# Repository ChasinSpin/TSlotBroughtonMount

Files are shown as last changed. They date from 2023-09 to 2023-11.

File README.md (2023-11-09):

# T-Slot Broughton Mount

#### Author: ChasinSpin

The T-Slot Broughton Mount is a fixed-position AltAz telescope mount designed primarily for pre-point asteroid occultations with smaller telescopes. It is similar to a tripod, but easier and more precise when adjusting. Better than 1-arcmin precision is easily achievable in practice.

This mount is inspired by the original Paver Mount design of John Broughton and has similar dimensions.

The design uses 2020 Aluminum T-Slot, 3D-Printed parts, and is easy to build.

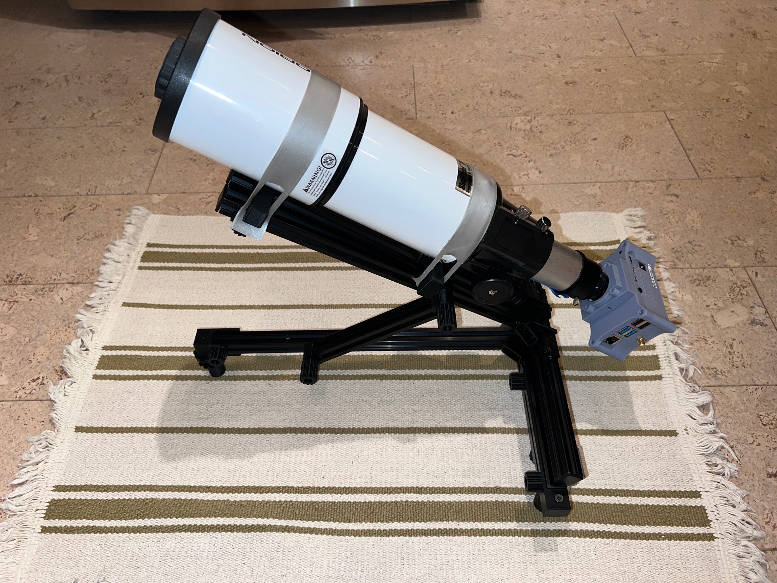
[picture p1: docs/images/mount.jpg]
T-Slot Broughton Mount


##### Overview:

* [Features](#features)
* [Supported Telescopes](#supported-telescopes)
* [Printing 3D Parts](#printing-3d-parts)
* [Azimuth Adjustment](#azimuth-adjustment)
* [Altitude Adjustment](#altitude-adjustment)
* [Collapsing For Transport](#collapsing-for-transport)
* [Marking Settings For Later Deployment](#marking-settings-forlater-deployment)
* [Attaching Telescopes](#attaching-telescopes)
* [High Altitudes near Zenith](#high-altitudes-near-zenith)
* [Use With 12inch Pavers](#use-with-12inch-pavers)
* [Extending For Larger Scopes](#extending-for-larger-scopes)
* [Paver Registration](#paver-registration)
* [Repeatability](repeatability)
* [Anti-Tip-Over Bar](anti-tip-over-bar)
* [Parts List](#parts-list)
* [Add-Ons](#add-ons)

##### Guides:

* [Assembly Guide](docs/assemblyguide.md)
* [Usage Guide](#usage-guide)

## Features

* Low profile
* Parametric design in [OpenSCAD](https://openscad.org). Can easily be adapted. 
* Full range (0-90 degrees in altitude - zenith works)
* Small and lightweight (3lb/1.375kg), ideal for air travel (can also be disassembled)
* Supports "pre-point later". (Set up, remove, and place back in position days later)
* Collapsable for transport (and can be put back to the previous AltAz position)
* Both coarse and fine adjustments for altitude and azimuth
* Rigid design
* Silver or black (black for stealth deployments)
* 2020 Aluminum T-Slot, using standard parts
* Easy to build (hacksaw, file, drill, 3D printed parts)
* Can be used with a 12" or 16" paver, staked piece of plywood for pre-positioning days prior
* Anti Tip-Over Bar
* Cost-effective
* Can be adjusted to better than 1-arcmin precision

## Supported Telescopes

Many small telescopes are supported, for example:

* Mighty Mini (IOTA) - (1/4-20 UNC standard tripod thread)
* Orion ST (Short Tube) 80mm
* If the scope is larger, the design can be expanded, see [Extending For Larger Scopes](extending-for-larger-scopes)

The [Astrid](https://github.com/ChasinSpin/astrid) astro imaging device is also supported.

## Printing 3D Parts

If you have a 3D filament printer, then you're good to go. It's also possible to order the parts printed for you via a 3D printing service. The parts are designed to be printed in PLA, but other materials can be used.

[STL Files](stl)

## Azimuth Adjustment

Coarse azimuth adjustments can be made by rotating the mount on the surface it's standing on.  Fine adjustments can be made with 2 fingers pushing against the 2 pieces of 2020 to displace the position and the thumbwheel can be used to tighten.

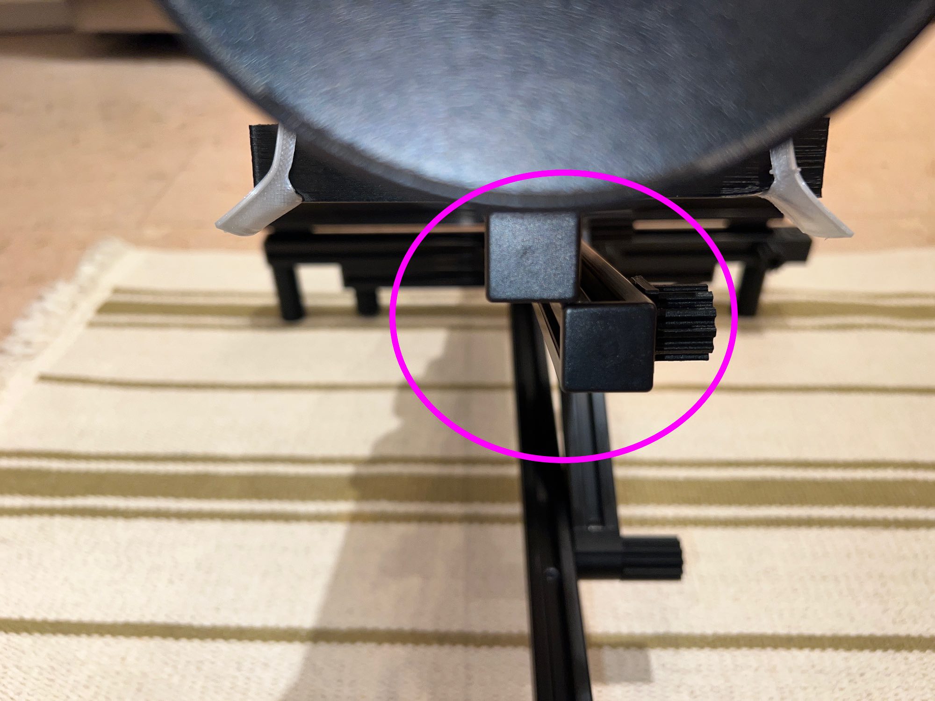
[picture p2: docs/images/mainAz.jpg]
Azimuth Adjustment


## Altitude Adjustment

Coarse altitude adjustments can be made by raising/lowering the altitude bar and tightening the knobs.  Fine adjustments can be made by using the screw in the foot at the front of the mount.

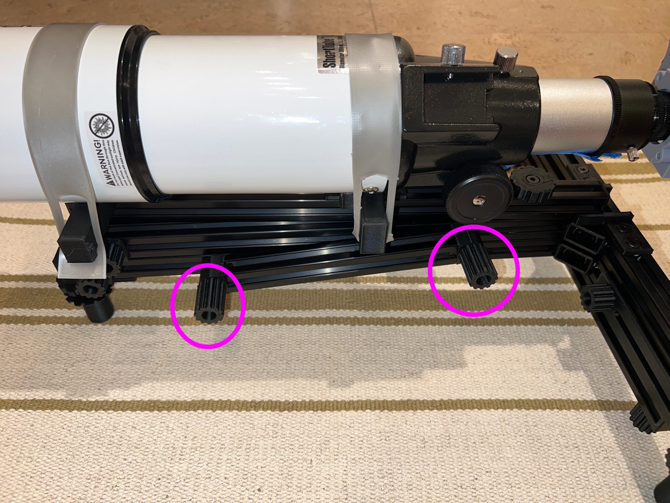
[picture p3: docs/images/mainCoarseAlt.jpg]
Coarse Altitude Adjustment

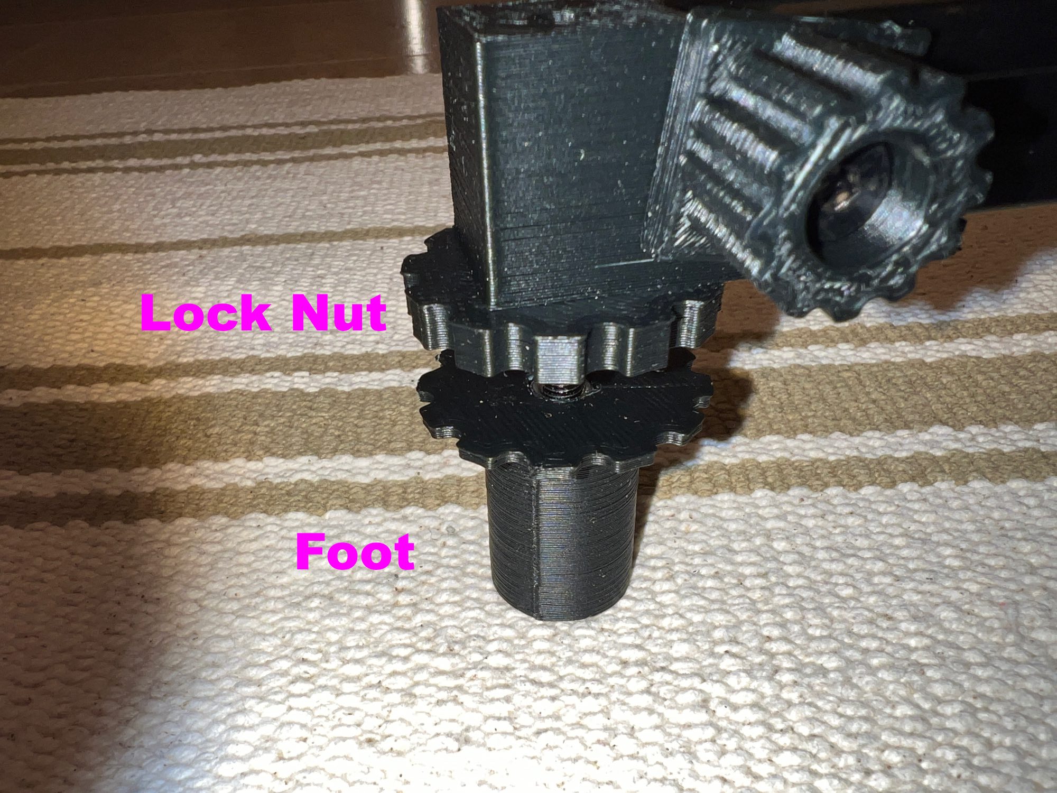
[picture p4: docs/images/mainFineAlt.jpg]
Fine Altitude Adjustment


## Collapsing For Transport

The mount can be completely collapsed for transport.  Additionally, if air traveling and an extremely minimal footprint is required, an Allen key can be used to detach the cross bars for transport.

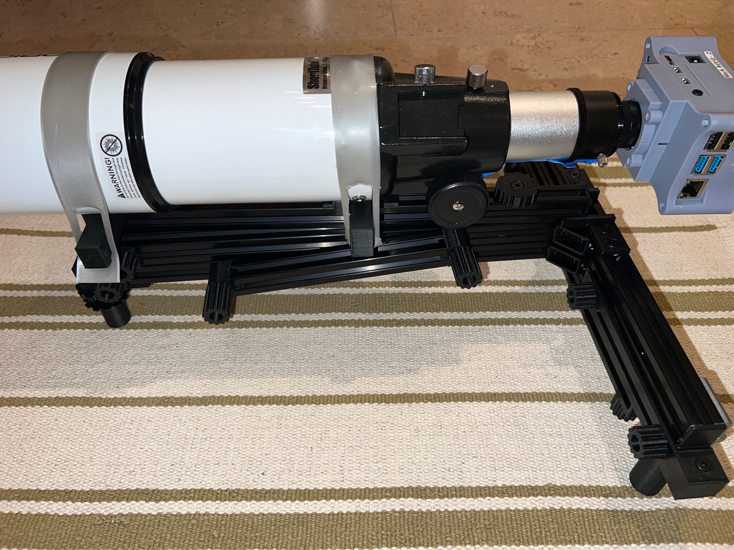
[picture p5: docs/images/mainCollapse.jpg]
Collapsed


## Marking Settings For Later Deployment

Move the altitude position markers up against the altitude bar to save the position, and tighten and disconnect the altitude bar.

An alternative is to use a 0.4mm Sharpie felt pen to mark the position of both ends of the altitude bar on the aluminum.  To remove the marking later, any type of alcohol can be used to remove.

The altitude fine adjustment foot can be locked in place using the lock wheel provided.

For azimuth, use the graduated scale near the front of the mount, and note the position (or take a photo).  Alternatively, calipers can be used to note the measurement for later.

## Attaching Telescopes

Telescopes can be attached via a stretchable band 3d printed from NinjaFlex or TPU.  Also, just a length of TPU/NinjaFlex filament, thick rubber band or strong elastic can be used.

## High Altitudes near Zenith

Due to the weight of the scope and the possibility of tip-over, for higher altitudes nearer to the zenith, the anti-tip-over bar should be swung out to prevent tip-over.  See [Anti-Tip-Over Bar](#anti-tip-over-bar)

## Use With 12inch Pavers

The original paver mount has its feet removed for placement on a 12-inch paver as the mount is larger than the paver.  The T-Slot Broughton Mount can be used the same way by removing the rear feet. Next, remove the front foot, and insert backward through the hole and T-Nut further back along the T-Slot to retain the fine altitude adjustment.

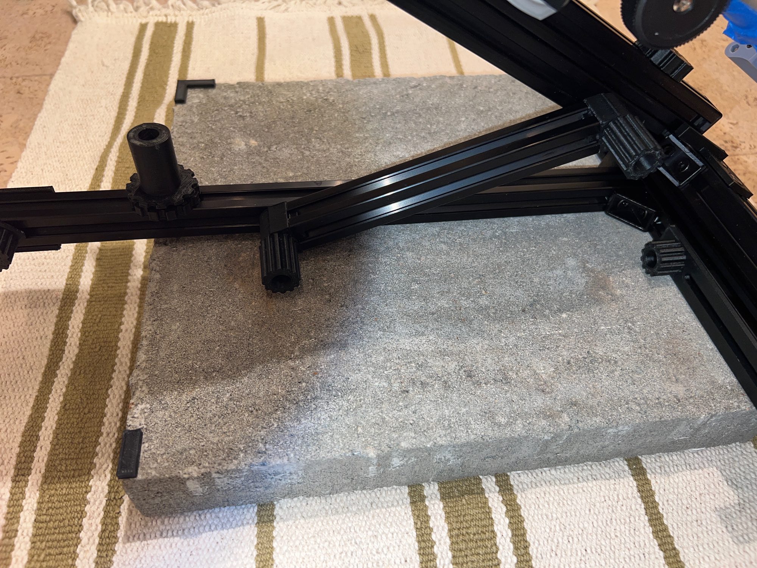
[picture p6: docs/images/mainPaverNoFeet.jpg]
Paver Without Feet


Another (better) option is to slide the rear feet so they are just under 12 inches apart.  Remove the Front Foot Lock from the Front Foot and insert the Front Foot into the hole and T-Nut further back from the front foot's regular location.  Now use the Front Foot Lock on top of the 2020 to lock down/remove play in the Front Foot.

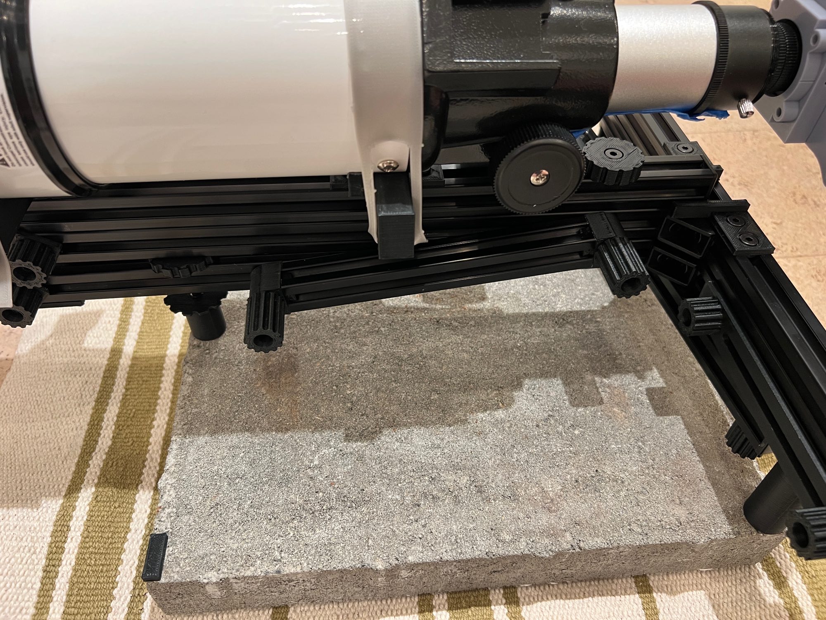
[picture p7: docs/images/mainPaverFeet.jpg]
Paver With Feet


To prevent tip over at high elevations with 12-inch paver, it's recommended to use the [Battery Platform](addons/BatteryPlatform/README.md).

## Extending For Larger Scopes

The design is extendable within sensible limits for larger telescopes, by increasing the length of the 2020 extrusion for parts ABC.

Extending

## Paver Registration

Repeatable registration of the mount feet with the paver can be accomplished by epoxying or super-gluing the paver makers at the edges of the paver.  Place the right-angled marker against the left corner and the straight marker against the same edge such that the left rear foot of the mount fits in the right-angled marker, and the right rear foot of the mount rests against the straight marker.

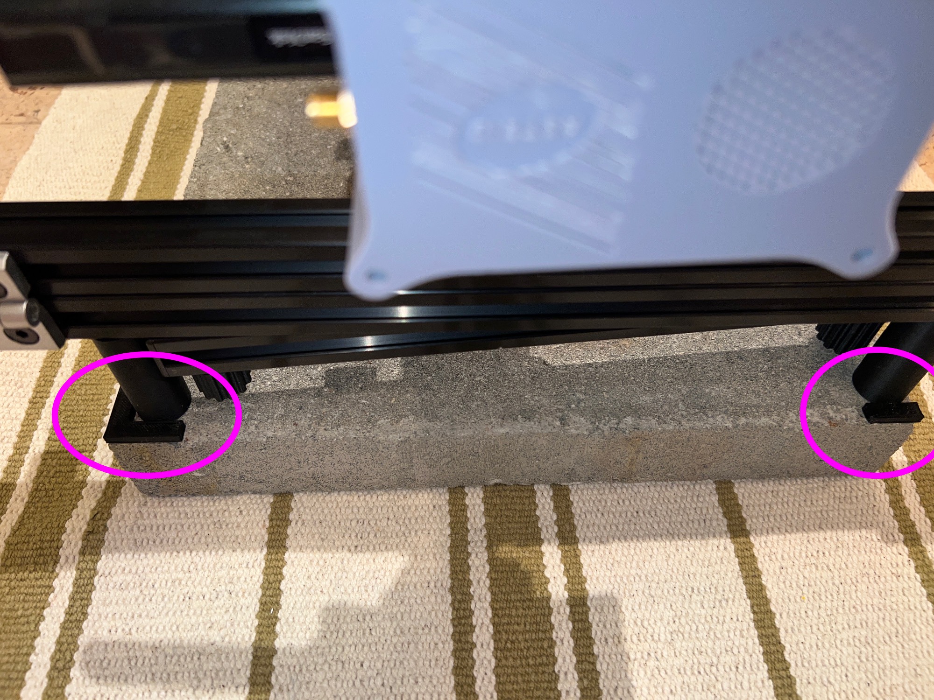
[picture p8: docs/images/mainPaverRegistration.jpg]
Paver Registration


## Repeatability

The following testing is with an Orion ST 80mm and IOTA Focal Reducer 0.5X with focal length 185mm and 1.543x1.154deg FOV.

**Initial** refers to the error after adjusting the mount to the pre-point location.  **Reposition** are subsequent measurements after repositioning the mount.

**Error Az/Alt** are in arc minutes and are the difference between where the telescope is pointing and the pre-point location of the target at that time.  **Error FOV** is the same error represented as a percentage of the Field of View, where the height of the field of view is 100%.

### Testing repeatability in pre-pointing with Astrid

After initial pre-point alignment and lockdown of the mount, the scope was picked up with the mount and placed back on the paver, to simulate a pre-point where the setup is removed and replaced days later.

| Step | Error Az (arcmin) | Error Alt (arcmin) | Error FOV |
| ---- | --- | --- | --- |
| Initial | -0.582 | -0.995 | 1.4% |
| Reposition | -3.690 | +0.638 | 5.3% |
| Reposition | -1.971 | +1.373 | 2.8% |
| Reposition | -1.710 | +1.539 | 2.5% |
| Reposition | +0.489 | +2.634 | 3.8% |
| Reposition | -6.155 | +2.172 | 8.9% |
| Reposition | -5.880 | +2.691 | 8.5% |
| Reposition | +3.263 | +3.217 | 4.7% |

### Testing repeatability for "pre-point later" with Astrid after mount collapse and telescope removal for transport

After initial pre-point alignment, the telescope was removed from the mount,
and the mount collapsed for transport.  The altitude bar position was maintained via the altitude bar markers, and the azimuth scale was noted.  The setup was then reassembled and aligned with the paver.

| Step | Error Az (arcmin) | Error Alt (arcmin) | Error FOV |
| ---- | --- | --- | --- |
| Initial | | | |
| TESTING PENDING

## Anti-Tip-Over Bar

The design has an anti-tip-over bar that can be swung out to the rear of the scope to prevent tip-over of the scope at high elevations.  The anti-tip-over bar does not fit the 12-inch paver due to the paver's small size, for this scenario please use the [Battery Platform](addons/BatteryPlatform/README.md) instead.

The Anti-Tip-Over Bar is optional and can be omitted for many occultations.

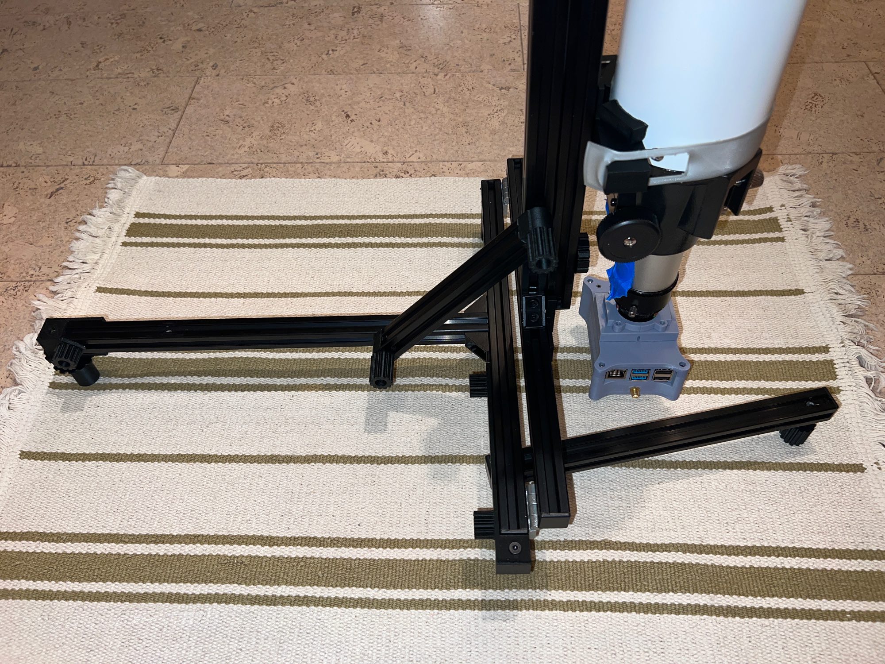
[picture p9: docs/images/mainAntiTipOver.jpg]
Anti-Tip-Over Bar


## Parts list

| Qty | Part | Description |
| --- | ---- | --- |
| 5 | 2020 x 360mm | [2020 EU STandard T-Slot](https://spool3d.ca/2020-aluminum-extrusion/) - 360mm Length (Silver or Black) |
| 1 | 2020 x 270mm | [2020 EU STandard T-Slot](https://spool3d.ca/2020-aluminum-extrusion/) - 270mm Length (Silver or Black) |
| 1 | 2020 x 160mm | [2020 EU STandard T-Slot](https://spool3d.ca/2020-aluminum-extrusion/) - 160mm Length (Silver or Black) |
| | | Note above T-Slot can be purchased as a 1 x 1.5m and 1 x 1m and cut to size or 3 x 1m | 
| 4 | 2020 Corner Bracket | [2020 Aluminum Corner Bracket Small](https://spool3d.ca/2020-aluminum-corner-bracket-small/) (Silver of Black) |
| 2 | 2020 Hinge | [2020 Aluminum Hinge](https://spool3d.ca/2020-aluminum-hinge/) (Silver or Black) |
| 28 | M5 x 8mm | [M5 Low Profile Bolt](https://spool3d.ca/m5-low-profile-screws/) - 8mm Length - Dimensions: (head diameter = 8.8mm, head thickness = 1.7mm) |
| 2 | M5 x 15mm | [M5 Low Profile Bolt](https://spool3d.ca/m5-low-profile-screws/) - 15mm Length - Dimensions: (head diameter = 8.8mm, head thickness = 1.7mm) |
| 4 | M5 x 35mm | [M5 Low Profile Bolt](https://spool3d.ca/m5-low-profile-screws/) - 35mm Length - Dimensions: (head diameter = 8.8mm, head thickness = 1.7mm) |
| 1 | M5 x 45mm | [M5 Low Profile Bolt](https://spool3d.ca/m5-low-profile-screws/) - 45mm Length - Dimensions: (head diameter = 8.8mm, head thickness = 1.7mm) |
| 1 | M5 x 50mm | [M5 Low Profile Bolt](https://spool3d.ca/m5-low-profile-screws/) - 50mm Length - Dimensions: (head diameter = 8.8mm, head thickness = 1.7mm) |
| 36 | M5 T-Nut | [M5 Sliding T-Nut](https://spool3d.ca/m5-sliding-t-nut/). Note, these are not twist in or "hammer head" T-Nuts, i.e. these are regular T-Nuts that won't fall out of the T-Slot.
| 10 | M5 Nut | M5 Nut - Dimensions: (diameter =  9mm point to point, thickness = 3.9mm) |
| 10 | End Cap | [Aluminum Extrusion Plastic Cap](https://spool3d.ca/aluminum-extrusion-plastic-cap/) |
| 1 | 3D Plate1 | Plate 1 3D-Printed Parts PLA |
| 1 | 3D Plate2 | Plate 2 3D-Printed Parts PLA |
| 1 | 3D Mount | 3D-Printed Mount PLA, e.g. Mount Orion ST 80mm or 1/4" Mount |
| 1 | 3D Bands | Bands 3D-Printed TPU/NinjaFlex to hold Orion ST 80mm telescope or strong rubber bands |
| 1 | 1/4-20 UNC Bolt | 1/4-20 UNC Bolt (regular tripod bolt) for 1/4 inch tripod mount if used) |
| 1 | Double Sided Tape | Permanent double-sided (e.g. Scotch Extreme Mounting Tape or Hot Glue) to attach telescope slide stops to telescope (Orion ST 80mm) |

**Note: All bolts are measured from the tip to the start of the head flange and do not include the thickness of the head.**

## Add-Ons

T-Slot is highly configurable.  If you design some fittings to work with this mount for telescopes, accessories, or anything else... please use [OpenSCAD](https://openscad.org) to design so that it is parametric and upload it to GitHub with a picture and README.md as a pull request, so others can benefit.  All submissions are assumed to be open source and under the MIT license.

[List of Add-Ons](/addons/README.md)

## Guides

* [Assembly Guide](docs/assemblyguide.md)
* [Usage Guide](docs/usageguide.md)
* [Troubleshooting Guide](docs/troubleshootingguide.md)

## Credits

* John Broughton - Inspiration from the original Paver Mount
* Steve Preston - Dimensions and scope configuration

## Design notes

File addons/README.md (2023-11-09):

# Add-Ons

T-Slot is highly configurable. If you design some fittings to work with this mount for telescopes, accessories, or anything else... please use OpenSCAD to design so that it is parametric and upload it to GitHub with a picture and README.md as a pull request, so others can benefit. All submissions are assumed to be open source and under the MIT license.

Available add-ons:

| Author | Summary | Description | Link |
| --- | --- | --- | ---- |
| ChasinSpin | Magnetic GPS Antenna | Retractable arm to hold a magnetic GPS antenna. | [MagGpsAntenna](MagGpsAntenna/README.md) |
| ChasinSpin | Battery Platform | Detachable platform to serve as weight and location for battery. | [BatteryPlatform](BatteryPlatform/README.md) |

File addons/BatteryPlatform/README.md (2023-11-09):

# Battery Platform

Detachable platform to serve as weight and a location to place the battery.

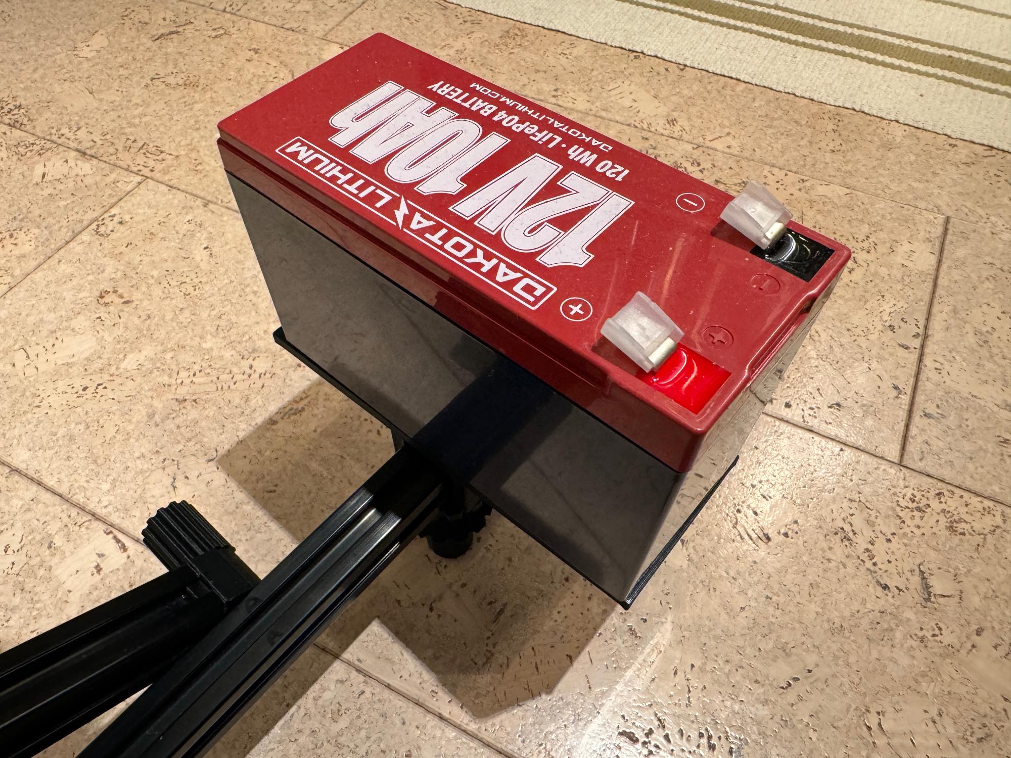
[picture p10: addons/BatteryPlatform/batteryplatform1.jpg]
Battery Platform With Battery

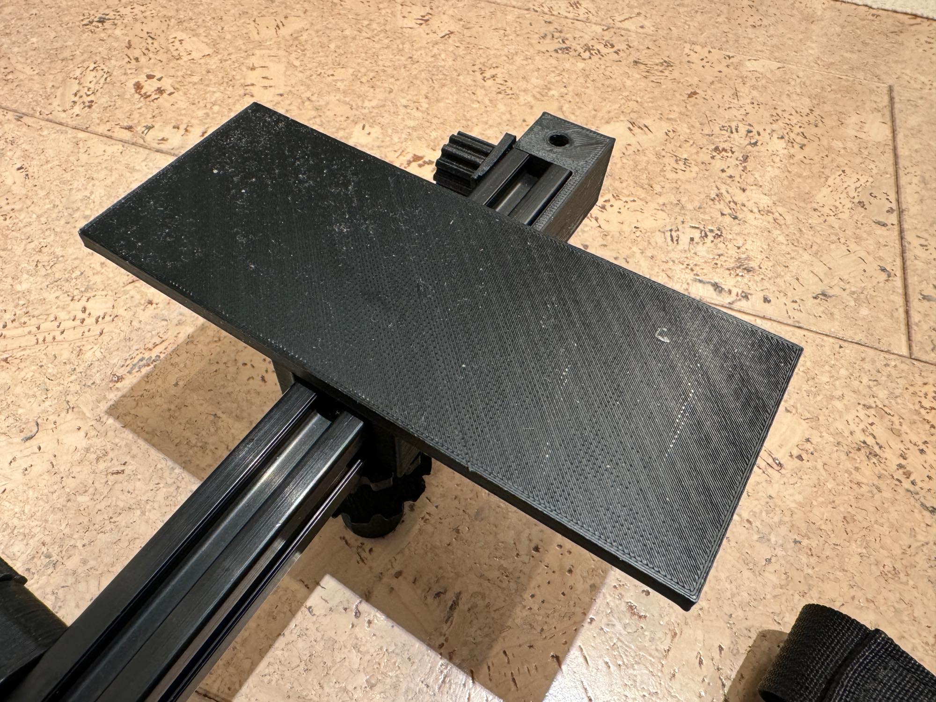
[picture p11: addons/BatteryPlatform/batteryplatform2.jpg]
Battery Platform Without Battery


## Parts

| Qty | Part | Description |
| --- | ---- | --- |
| 1 | 3D Printed Parts | The 3D printed parts in the STL below.  Print 15% fill and with support |

## Assembly

Place on top of the T-Slot
 
## Files

* [STL](batteryplatform.stl)
* [OpenScad](batteryplatform.scad)

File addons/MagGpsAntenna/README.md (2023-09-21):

# Magnetic GPS Antenna Holder

Retractable arm to hold a magnetic GPS antenna.

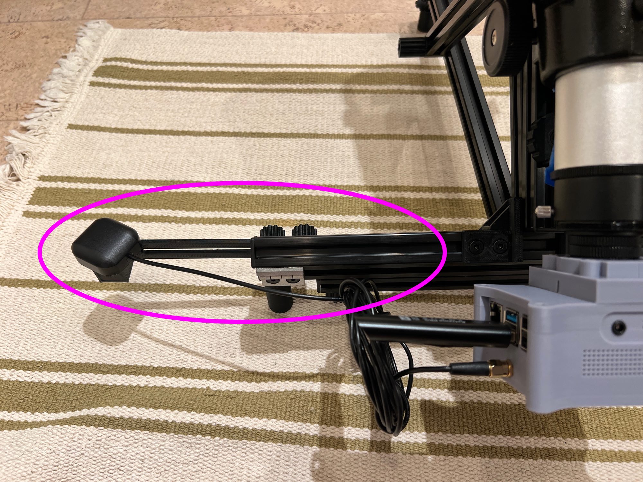
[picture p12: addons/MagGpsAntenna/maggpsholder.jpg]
Mag GPS Holder


## Parts

| Qty | Part | Description |
| --- | ---- | --- |
| 1 | 3D Printed Parts | The 3D printed parts in the STL below.  Print 15% fill and with support |
| 1 | M5 x 8mm | [M5 Low Profile Bolt](https://spool3d.ca/m5-low-profile-screws/) - 8mm Length - Dimensions: (head diameter = 8.8mm, head thickness = 1.7mm) |
| 2 | M5 x 15mm | [M5 Low Profile Bolt](https://spool3d.ca/m5-low-profile-screws/) - 15mm Length - Dimensions: (head diameter = 8.8mm, head thickness = 1.7mm) |
| 2 | M5 T-Nut | [M5 Sliding T-Nut](https://spool3d.ca/m5-sliding-t-nut/). Note, these are not twist in or "hammer head" T-Nuts, i.e. these are regular T-Nuts that won't fall out of the T-Slot.
| 2 | M5 Nut | M5 Nut - Dimensions: (diameter =  9mm point to point, thickness = 3.9mm) |

## Assembly

Screw a M5x8mm bolt into the tapered hole, the antenna magnetically attaches to this.  Use 2 x M5x8mm and 2 x T-Nut in the remaining holes (one of which is a long hole.

Assembly the knobs with the M5 nuts and M5x15mm bolts.  Screw the knob through the holes into the T nut in the 2020 profile.
 
## Files

* [STL](maggpsholder.stl)
* [OpenScad](maggpsholder.scad)

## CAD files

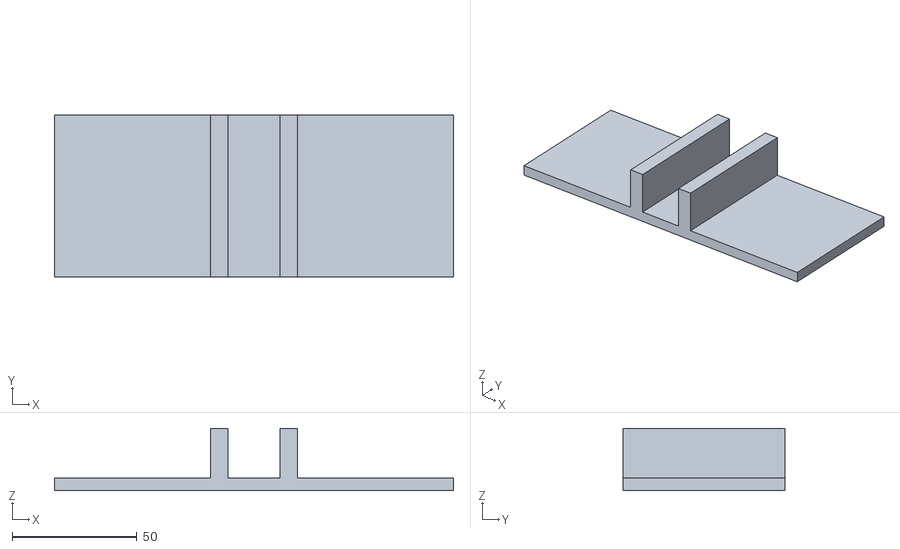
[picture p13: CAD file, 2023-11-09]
addons/BatteryPlatform/batteryplatform.stl
160.0 x 65.0 x 25.0

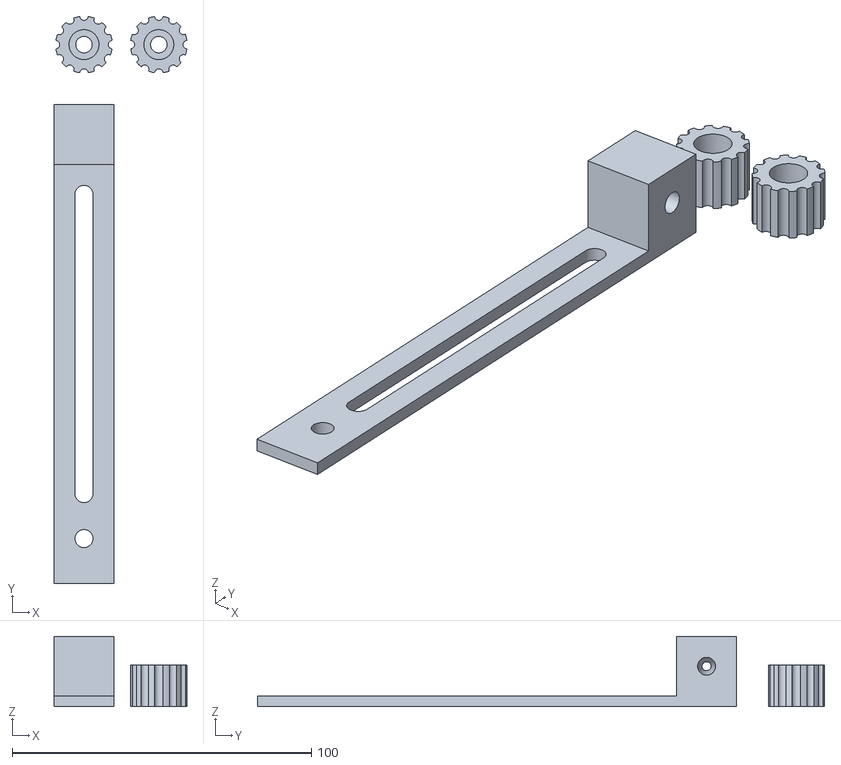
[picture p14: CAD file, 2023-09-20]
addons/MagGpsAntenna/maggpsholder.stl
44.4 x 189.4 x 23.5

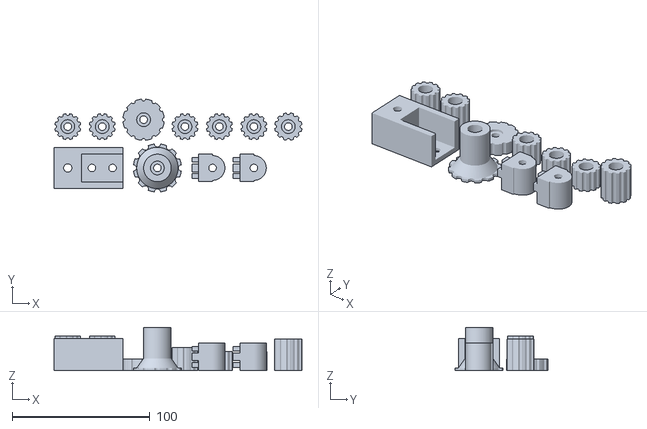
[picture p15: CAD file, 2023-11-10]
stl/plate2.stl
179.9 x 67.3 x 31.5

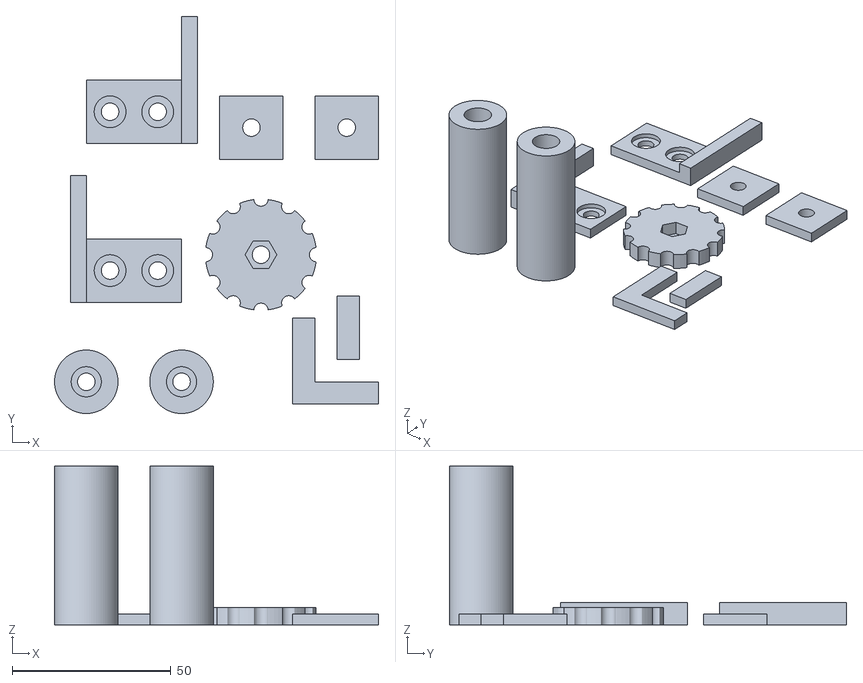
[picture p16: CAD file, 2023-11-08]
stl/plate1.stl
102.0 x 125.0 x 50.0

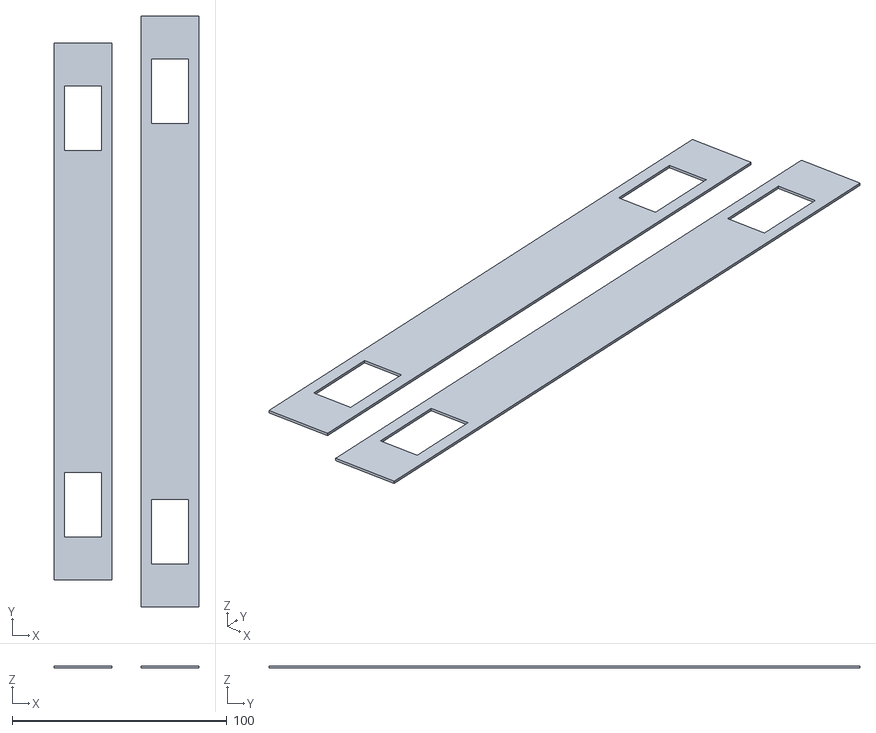
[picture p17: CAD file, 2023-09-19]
stl/mountBandsOrionST80.stl
67.5 x 275.0 x 1.00

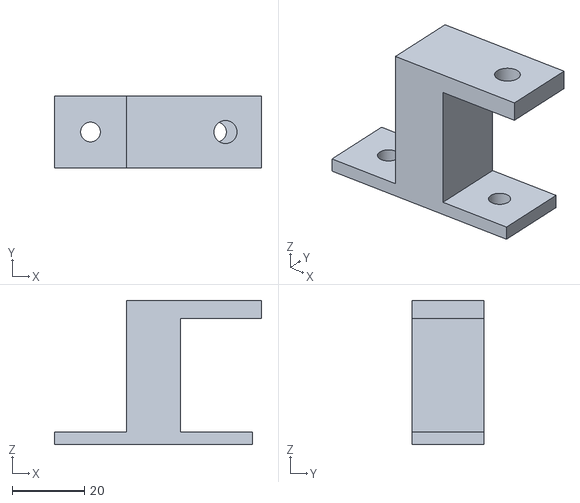
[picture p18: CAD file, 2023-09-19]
stl/mountQuarterInch.stl
57.5 x 20.0 x 40.0

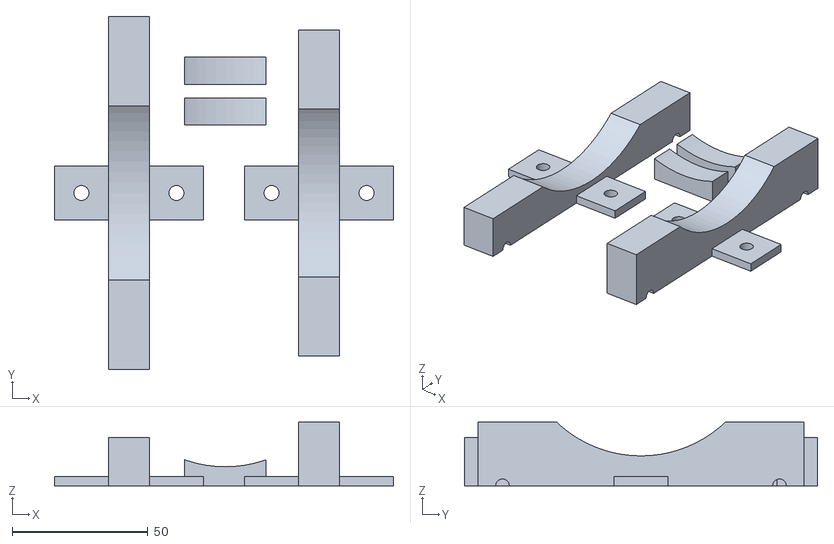
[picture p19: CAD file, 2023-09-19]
stl/mountRestsOrionST80.stl
125.0 x 130.0 x 23.4

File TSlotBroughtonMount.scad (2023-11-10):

// Copyright: ChasinSpin, 2023
// License: MIT License
//
// Suggested print speed for Creality Ender 5: Print Speed: 60mm/s (bottom 20mm/s) Travel Speed: 150mm/s
//
// Part 0 = PLA 15% fill, no support (Parts 2, 6, 10, 12, 14)
// Part 1 = PLA 15% fill, support (Parts 3, 4, 7, 8, 9, 11, 13, 16)
// Part 2 = PLA 15% fill, no support
// Part 3 = PLA 15% fill, support
// Part 4 = PLA 15% fill, support
// Part 5 = PLA 15% fill, no support
// Part 6 = PLA 15% fill, no support
// Part 7 = PLA 15% fill, support
// Part 8 = PLA 15% fill, support
// Part 9 = PLA 15% fill, support
// Part 10 = PLA 15% fill, no support
// Part 11 = PLA 15% fill, support
// Part 12 = PLA 15% fill, no support
// Part 13 = PLA 15% fill, support
// Part 14 = PLA 15% fill, no support
// Part 15 = PLA 15% fill, no support
// Part 16 = PLA 15% fill, support
// Part 17 = Ninjaflex 30% fill, no support
// Part 18 = PLA 15% fill, no support (Parts 5, 15) 
// Part 19 = PLA 15% fill, support 

partNum                         = 1;    // 0 = Plate 1, 1 = Plate 2, 2 = Feet, 3 = Alt Foot Holder, 4 = Alt Foot, 5 = Telescope Supports, 6 = Az Stops, 7 = Alt Knobs, 8 = Rotator Knob, 9 = Extension Knob, 10 = Alt Lock Nut, 11 = Alt Bearing, 12 = Altitude Markers, 13 = Altitude Marker Knobs, 14 = Paver Markers, 15 = Telescope Slide Stop, 16 = Extension Foot, 17 = Orion ST 80mm Bands, 18 = Orion ST 80mm Mount, 19 = Quarter Inch Mount

full2020                        = 20;
half2020                        = full2020/2.0;

m5BoltDiameter                  = 5.5;
m5NutThickness                  = 4.5;
m5HeadThickness                 = 1.5;
m5NutDiameter                   = 10.0;
m5HeadDiameter                  = 10.0;

footBoltHeadDiameter            = 9.5;
footBoltDiameter                = m5BoltDiameter;
footDiameter                    = 20;
footLengthMain                  = 50;
footFlangeThickness             = 3.5;

doubleFlangeHolePos             = 7.5;
doubleFlangeHoleDia             = m5BoltDiameter;
doubleFlangeHoleFlangeLength    = 30.0;
doubleFlangeBoltHeadThickness   = m5HeadThickness;
doubleFlangeBoltHeadDiameter    = m5HeadDiameter;
doubleFlangeThickness           = 3.5;

singleFlangeHolePos             = half2020;
singleFlangeHoleDia             = m5BoltDiameter;
singleFlangeHoleFlangeLength    = full2020;
singleFlangeBoltHeadThickness   = m5HeadThickness;
singleFlangeBoltHeadDiameter    = m5HeadDiameter;
singleFlangeThickness           = 3.5;

altFootHolderHolePos            = 7.5;
altFootHolderHoleDia            = m5BoltDiameter;
altFootHolderHoleFlangeLength   = 30;
altFootHolderMainHoleDia        = 6.0;
altFootHolderNutDia             = m5NutDiameter;
altFootHolderNutThickness       = m5NutThickness;
altFootHolderFlangeThickness    = 3.5;
altFootHolderFlangeThickness2   = altFootHolderFlangeThickness + 1;
altFootHolder2020Clearance      = 0.25;


altFootFootDiameter             = 20.0;
altFootLength                   = 50 - 18.5;
altFootMainHoleDia              = m5BoltDiameter;
altFootNutThickness             = m5NutThickness;
altFootNutDiameter              = m5NutDiameter;
altFootBoltHeadDiameter         = m5HeadDiameter;
altFootFlangeThickness          = 3.5;
altFootKnurledDiameter          = 35.0;
altFootKnurledThickness         = 2.0;
altFootKnurlDiameter            = 4.5;

altLockThickness                = m5NutThickness + 1.0;
altLockNutThickness             = m5NutThickness;
altLockNutDiameter              = m5NutDiameter;
altLockNutBoltDiameter          = m5BoltDiameter;

altBearingBoltDiameter = m5BoltDiameter;
altBearingDiameter     = full2020 - 2;
altBearingRetainerLength        = 5;
altBearingRetainerDimensions    = [altBearingRetainerLength, 5.5, 3.5];
altBearingRetainerOffset        = 4.15 + altBearingRetainerDimensions[2]/2;
altBearingPostDiameter          = 4.5;

restHeight                      = 15;
rest1Diameter                   = 100.0;
rest1Height                     = restHeight + 2.7;
rest1Length                     = rest1Diameter + 30;
rest1OffsetTube                 = rest1Diameter / 2 + 6;
rest2Diameter                   = 90.0;
rest2Height                     = restHeight + 2.7 + 5.7;
rest2Length                     = rest2Diameter + 30;
rest2OffsetTube                 = rest1OffsetTube;
restWidth                       = 15;
restBandNotchDiameter           = 5.0;
restBandNotchInset              = 9.0;
restBoltDiameter                = m5BoltDiameter;
restFlangeThickness             = 3.5;

telescopeSlideStopDiameter      = rest2Diameter;
telescopeSlideStopLength        = 30.0;
telescopeSlideStopHeight        = 10;
telescopeSlideStopThickness     = 10;
telescopeSlideStopOffsetZ       = -3;    

azStopDimensions                = [0.25 * full2020, full2020 * 2, doubleFlangeThickness * 2];

band1Length                     = 210;
band2Length                     = 235;
bandTabLength                   = 20;
bandWidth                       = restWidth + 12;
bandNotch                       = [restWidth + 2, 30];
bandThickness                   = 1;

altKnobDiameter                 = 19;
altKnobLength                   = 25;
altKnobBoltDiameter             = m5BoltDiameter;
altKnobNutDiameter              = m5NutDiameter;
altKnobNutThickness             = m5NutThickness;
altKnobBoltHeadDiameter         = m5HeadDiameter;
altKnobFlangeThickness          = 6.3;
altKnobKnurlDiameter            = 2.8;

altMarkerKnobLength             = 14;
altMarkerKnobFlangeThickness    = 3.5;

extensionKnobLength             = 17.0;

rotatorKnobDiameter             = 30.0;
rotatorKnobLength               = 8.6;
rotatorKnobFlangeThickness      = 2.5;

extensionFootKnobLength         = 50 - (full2020 + 7);
extensionFootKnobDiameter       = 20;
extensionFootKnobFlangeThickness= 12.3;

quarterInchMountRiserDimensions = [15, 20, 40];
quarterInchPlatformDimensions   = [30, quarterInchMountRiserDimensions[1], 5];
quarterInchHoleDiameter         = 0.25 * 25.6;
quarterInchHoleOffsetX          = 20;    

manifoldCorrection              = 0.01;
$fn                             = 80;



if ( partNum == 0 )
{
    // PLA 15% fill, no support (Parts 2, 6, 10, 12, 14)

    // Part 2
    rotate( [180, 0, 0] )
    {
        translate( [0, 0, -footLengthMain] )
            foot(footLengthMain);
        translate( [footDiameter * 1.5, 0, -footLengthMain] )
            foot(footLengthMain);
    }

    // Part 6
    translate( [0, 35, 0] )
    {
        azStop(true);
        translate( [0, full2020 * 2.5, 0] )
            azStop(false);
    }

    // Part 10
    translate( [55, 40, 0] )
        altLockNut();
    
    // Part 12
    translate( [42, 80, 0] )
    {
        singleFlange(false);
        translate( [full2020 * 1.5, 0, 0] )
            singleFlange(false);
    }
    
    // Part 14
    translate( [65, 0, 0] )
        paverMarkers();
}
else if (partNum == 1)
{
    // PLA 15% fill, support (Parts 3, 4, 7, 8, 9, 11, 13, 16)
    
    // Part 3
    altFootHolder();
    
    // Part 4

    translate( [55, 0, 0] )
        translate( [0, 0, altFootLength] )
            rotate( [180, 0, 0] )
                altFoot();
    
    // Part 7
    translate( [-10, 30, 0] )
    {
        knurledKnob(altKnobDiameter, altKnobLength, altKnobFlangeThickness);
        translate( [25, 0, 0] )
            knurledKnob(altKnobDiameter, altKnobLength, altKnobFlangeThickness);
    }

    // Part 8
    translate( [45, 35, 0] )
        knurledKnob(rotatorKnobDiameter, rotatorKnobLength, rotatorKnobFlangeThickness);

    // Part 9
    translate( [75, 30, 0] )
        knurledKnob(altKnobDiameter, extensionKnobLength, altKnobFlangeThickness);

    // Part 11
    translate( [85, 0, 0] )
    {
        altBearing();
        translate( [full2020 * 1.5, 0, 0] )
            altBearing();
    }
 
    // Part 13
    translate( [100, 30, 0] )
    {
        knurledKnob(altKnobDiameter, altMarkerKnobLength, altMarkerKnobFlangeThickness);
        translate( [25, 0, 0] )
            knurledKnob(altKnobDiameter, altMarkerKnobLength, altMarkerKnobFlangeThickness);
    }
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

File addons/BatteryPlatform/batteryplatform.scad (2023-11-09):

// Copyright: ChasinSpin, 2023
// License: MIT License

// Print 15% Fill No Support

full2020                        = 20;
clearance2020                   = 1;
batteryBaseDimensions           = [160, 65, 5];
flange2020Thickness             = 7;


batteryPlatform();


module batteryPlatform()
{
    translate( [0, 0, batteryBaseDimensions[2]/2] )
        cube(batteryBaseDimensions, center = true);
    
    translate( [0, 0, batteryBaseDimensions[2] + full2020/2] )
    {
        flangeHalfDistance = ((full2020 + clearance2020) + flange2020Thickness)/2;
        translate( [-flangeHalfDistance, 0, 0] )
            cube( [flange2020Thickness, batteryBaseDimensions[1], full2020], center=true);
        translate( [flangeHalfDistance, 0, 0] )
            cube( [flange2020Thickness, batteryBaseDimensions[1], full2020], center=true);
    }
}


manifoldCorrection              = 0.01;
$fn                             = 80;

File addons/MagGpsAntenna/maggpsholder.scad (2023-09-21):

// Copyright: ChasinSpin, 2023
// License: MIT License

// Print 15% Fill With Support

// Requires:
//      1 x M5x8mm Low Profile Bolt
//      2 x M5x15mm Low Profile Bolt
//      2 x T-Nut
//      2 x M5 Nut
//
//      Screw a M5x8mm bolt into the tapered hole, the antenna magnetically attaches to that.
//      2 x M5x8mm and 2 x T-Nut are used in the hole in the long part and in the lozenge hole.
//      M5 nut and M5x15mm bolt are used in the knobs.

full2020                        = 20;

boltHoleDiameter                = 6;

m5BoltDiameter                  = 5.5;
m5HeadThickness                 = 1.5;
m5HeadDiameter                  = 10.0;
m5NutThickness                  = 4.5;
m5NutDiameter                   = 10.0;

holderLength                    = 140;
holderThickness                 = 3.5;

offsetHole1                     = 15;

lozengeHoleLength               = 100.0;
offsetLozengeHole               = 10;

magBoltInnerDiameter            = 3.0;
magBoltOuterDiameter            = 6.0;

altKnobDiameter                 = 19;
altKnobBoltDiameter             = m5BoltDiameter;
altKnobNutDiameter              = m5NutDiameter;
altKnobNutThickness             = m5NutThickness;
altKnobBoltHeadDiameter         = m5HeadDiameter;
altKnobKnurlDiameter            = 2.8;

altMarkerKnobLength             = 14;
altMarkerKnobFlangeThickness    = 3.5;

manifoldCorrection              = 0.01;
$fn                             = 80;


translate( [0, 0, holderThickness] )
    rotate( [180, 0, 0] )
        maggpsholder();
        
translate( [0, 40, 0] )
{
    knurledKnob(altKnobDiameter, altMarkerKnobLength, altMarkerKnobFlangeThickness);
    translate( [25, 0, 0] )
        knurledKnob(altKnobDiameter, altMarkerKnobLength, altMarkerKnobFlangeThickness);
}



module maggpsholder()
{
    difference()
    {
        // Main length
        translate( [-full2020/2, 0, 0] )
            cube( [full2020, holderLength, holderThickness] );
    
        // Bolt hole
        translate( [0, holderLength - offsetHole1, -manifoldCorrection] )
            cylinder(d=boltHoleDiameter, h = holderThickness + manifoldCorrection * 2);
        
        // Lozenge hole
        translate( [-boltHoleDiameter/2, offsetLozengeHole, -manifoldCorrection] )
            cube( [boltHoleDiameter, lozengeHoleLength, holderThickness + manifoldCorrection * 2] );
        
        // Rounded lozenge
        translate( [0, offsetLozengeHole, -manifoldCorrection] )
            cylinder(d = boltHoleDiameter, h = holderThickness + manifoldCorrection * 2);

        translate( [0, lozengeHoleLength + offsetLozengeHole, -manifoldCorrection] )
            cylinder(d = boltHoleDiameter, h = holderThickness + manifoldCorrection * 2);
    }
    
    difference()
    {
        // End block
        translate( [-full2020/2, -full2020, -full2020] )
            cube( [full2020, full2020, full2020 + holderThickness] );
    
        // Bolt Hole Tapered
        translate( [0, -full2020/2, -full2020/2] )
            rotate( [0, 90, 0] )
                cylinder(d1 = magBoltInnerDiameter, d2 = magBoltOuterDiameter, h = full2020 + manifoldCorrection * 2, center = true);
    }
}



module knurledKnob(diameter, length, flangeThickness)
{
    difference()
    {
        // Main Cylinder
        cylinder(d = diameter, h = length);
        
        // Main hole
        translate( [0, 0, -manifoldCorrection] )
            cylinder(d = altKnobBoltDiameter, h = length + manifoldCorrection * 2);
        
        // Nut
        translate( [0, 0, -manifoldCorrection] )
           cylinder(d = altKnobNutDiameter, h = altKnobNutThickness + manifoldCorrection, $fn = 6);

        // Head recess
        headRecessLength = length - (altKnobNutThickness + flangeThickness);
        translate( [0, 0, length - headRecessLength + manifoldCorrection] )
            cylinder(d = altKnobBoltHeadDiameter, h = headRecessLength);
        
        // Knurl
        for ( r = [0:30:360] )
            rotate( [0, 0, r] )
                translate( [diameter/2, 0, -manifoldCorrection] )
                    cylinder(d = altKnobKnurlDiameter, h = length + manifoldCorrection * 2);            
    }
}

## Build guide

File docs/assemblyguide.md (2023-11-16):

# Assembly Guide

## Tools Required:

* Hobby Knife
* Hacksaw and Miter Box
* Drill Bit 5mm (ideally) or 13/64" (slightly larger)
* Drill
* Metal File or Coarse Belt Sander
* Coarse Sand Paper
* Superglue
* Pliers
* 3mm Allen Key
* Double Sided Permanent Tape

## Important Warnings: 
1. Fine aluminum dust/chips created by sanding, cutting, and filing can combust and be an explosion hazard when provided with an ignition source.  Clean the work area frequently and avoid ignition sources.

2. Wear protective eyewear/gear.

It's recommended that foam/felt or other materials are not used on the telescope saddles if the mount is intended to be used for "pre-point later" so that the telescope will be in the same place when reassembled.  The telescope stops should be used instead to prevent the telescope from slipping backward at higher elevations.

## Part Identification

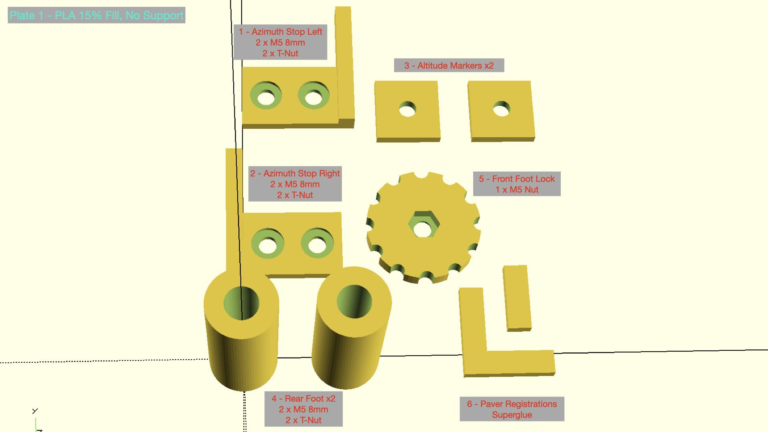
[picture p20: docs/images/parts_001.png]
Parts1

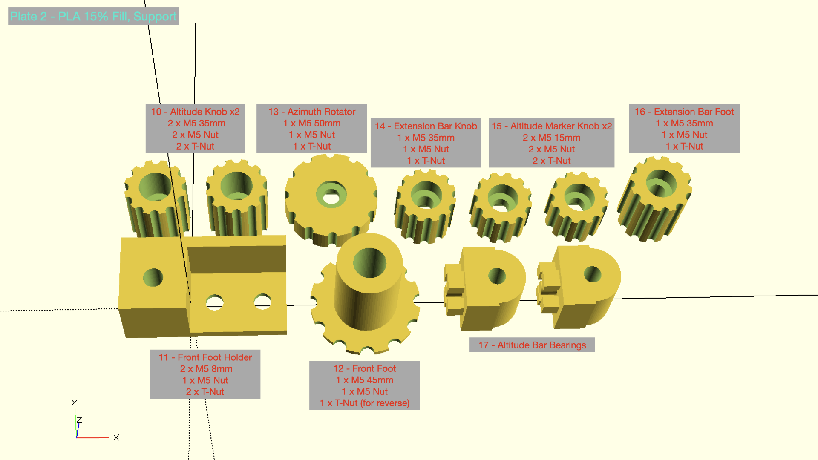
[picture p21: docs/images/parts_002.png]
Parts2

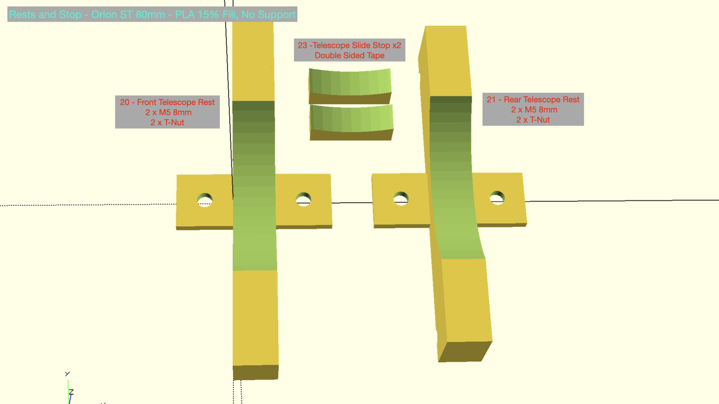
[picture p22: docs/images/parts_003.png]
Parts3

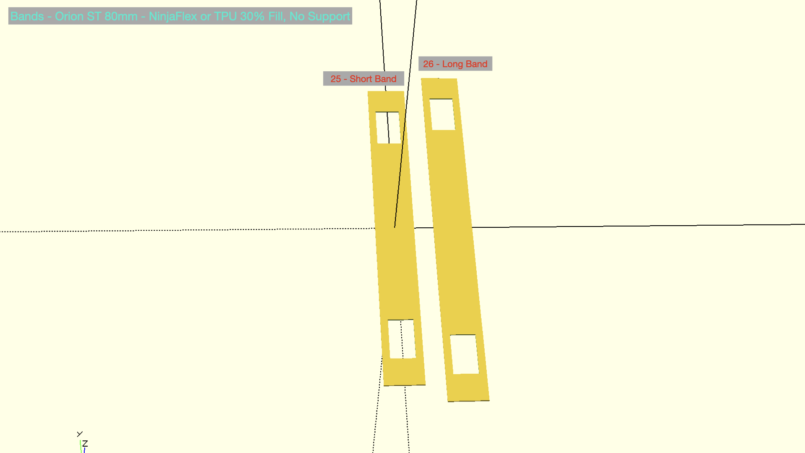
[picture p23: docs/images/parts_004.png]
Parts4

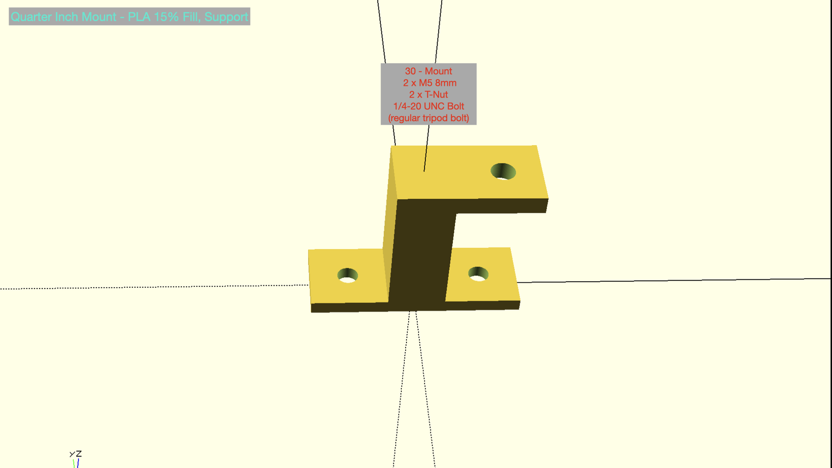
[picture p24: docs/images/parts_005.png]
Parts5


## Instructions

From Step 3, assembly time takes about 50 minutes.

### 2020 T-Slot Profile Cut Summary (see steps below for more details)

| Part # | Length | 5mm Drill Holes |
| --- | --- | --- |
| A | 360mm | 1 @ 100mm from end |
| B | 360mm | 1 @ 51mmm from end |
| C | 360mm | 1 @ 51mmm from end |
| D | 360mm | No Holes |
| E | 360mm | No Holes |
| F | 160mm | No Holes |
| G | 270mm | 2 @ 13mm (from each end) |

Note: For part G, the 2 drill holes are in the same orinetation.

### Step 1

Cut the 2020 T-Slot Profile to length.  Hacksaw is the safest way to this and can be squared off with filing or sanding.  

Miter Saw (Chop Saw) with a blade designed for cutting aluminum profile (Non-Ferrous) can also be used for clean straight cuts, however it carries a certain amount of risk of bodily harm so appropriate safety gear should be used, parts anchored down etc.  If you wish to use this approach, please research appropriately before embarking.

Step 1

Cut 7 lengths:

* ABCDE - 5 x 360mm - (Labeled ABCDE)
* F - 1 x 160mm (Coarse Altitude Bar)
* G - 1 x 270mm (Anti-Tip-Over Bar)

Deburr/sand any sharp edges.

### Step 2

Using the Part Identification Guide Above, locate the Altitude Bar Bearings (17).

Use super glue to glue the bearings to the ends of the Coarse Altitude Bar, ensuring that they are flush with the end and both holes are oriented in the same direction.  You may need to trim the bearings carefully with a hobby knife to sit flush with the end.

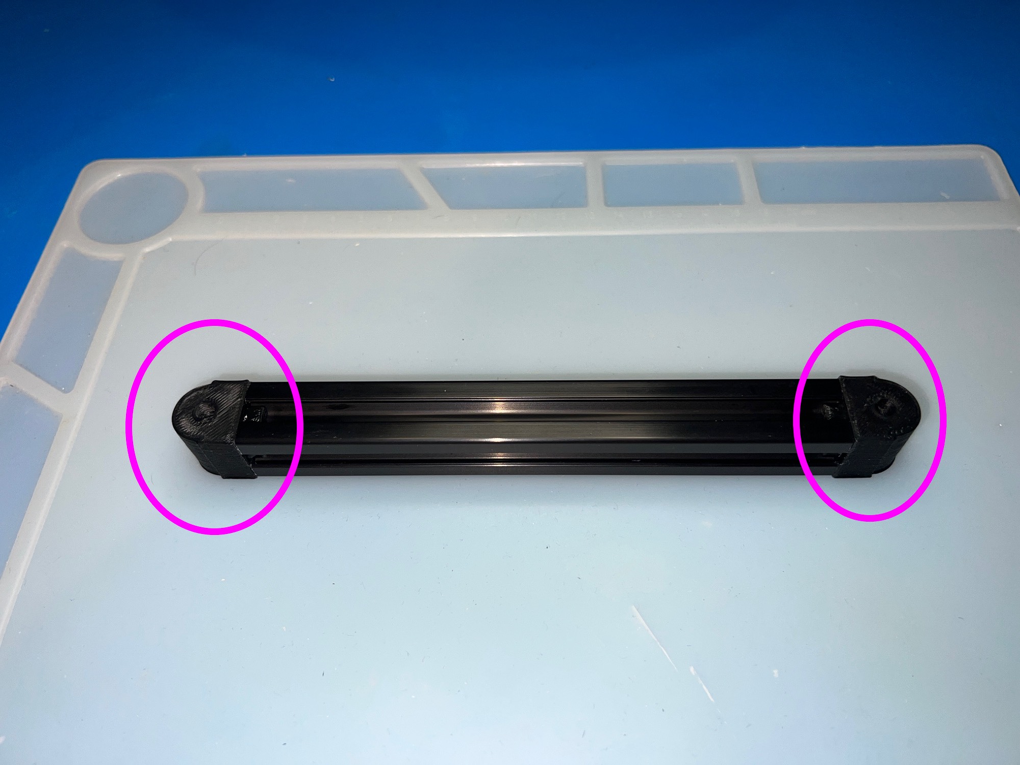
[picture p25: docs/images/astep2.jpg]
Step 2


Let dry a couple of hours before handling.

### Step 3

Find Plate 1 - 5 (Front Foot Lock) and Plate 2 - 11 (Front Foot Holder).  Insert an M5 Nut into each of the hex nut holders and make sure the are square with the surface and fully inserted.  Now put a drop of super glue on opposite sides where the nut abuts the plastic, the super glue will wick into the gap.  Be careful not to use too much superglue and contaminate the threads.

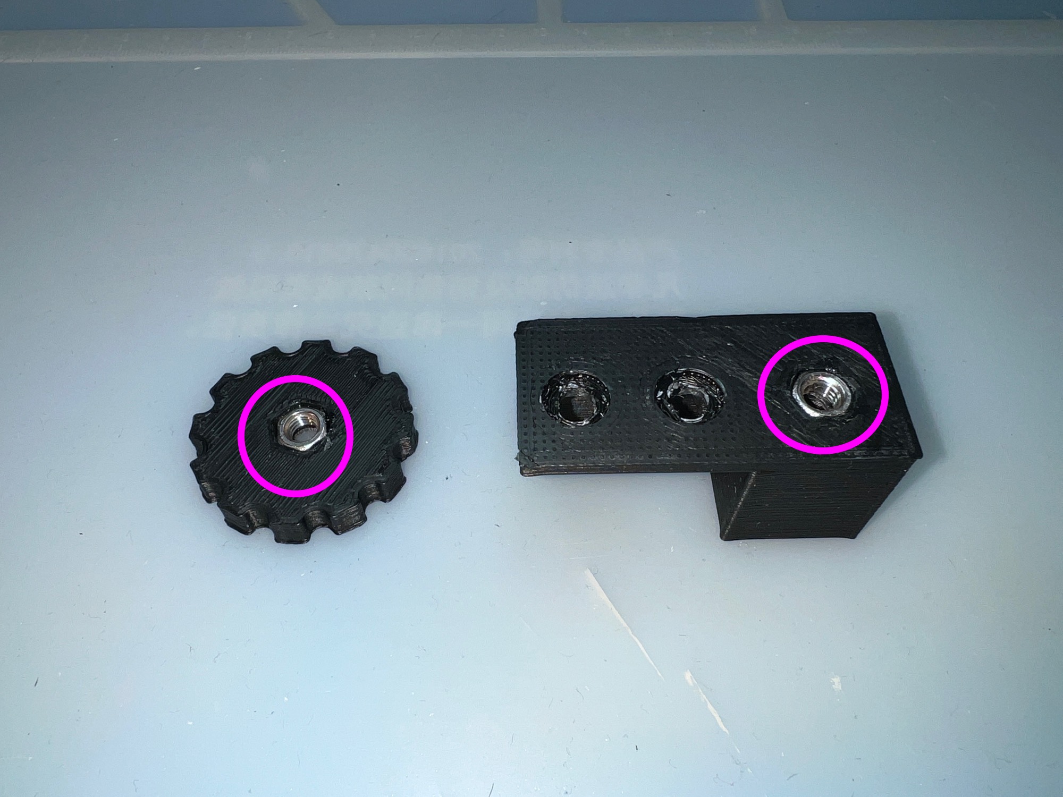
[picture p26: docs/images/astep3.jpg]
Step 3


Let dry a couple of hours before handling.

### Step 4

From Plate 1 locate parts 10, 12, 13, 14, 15, 16. Make sure the holes are clear of plastic filament, and insert an M5 Nut into each hex nut holder.  Now insert the appropriate bolt length (indicated on the Plate 2 diagram), and tighten fully using an Allen key.  (Do Not Use Superglue).  Note parts 10 and 16 are similar in length and part 16 is slightly shorter than 10.

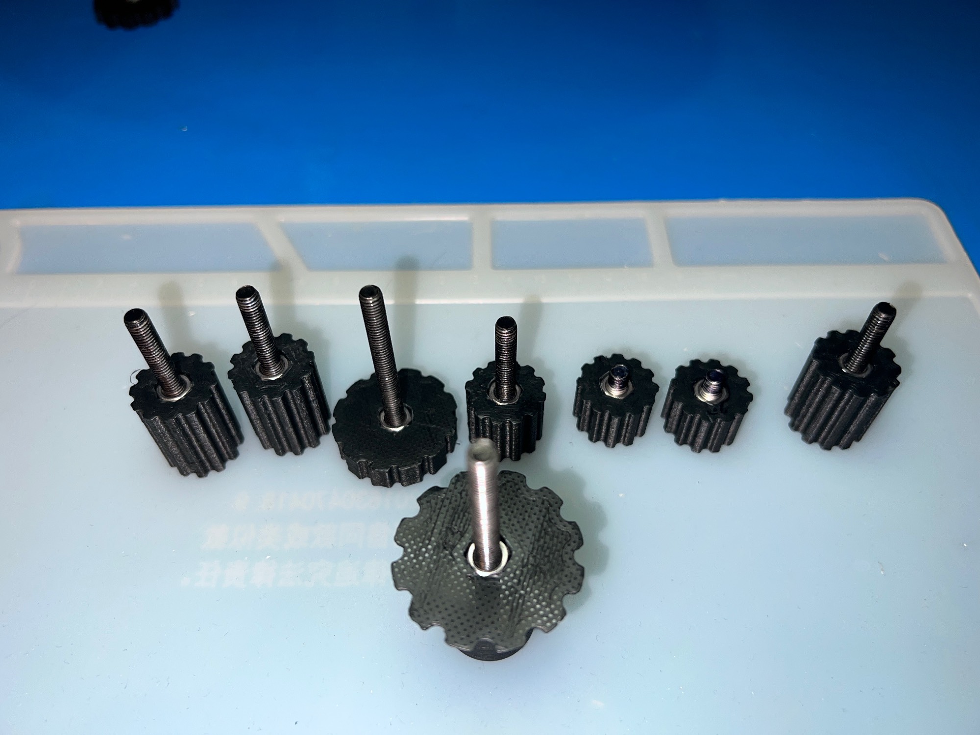
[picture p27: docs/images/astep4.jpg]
Step 4


### Step 5

Take a piece of 360mm profile and drill a 5mm hole 3 29/32"/ 100mm from the end. Label Part A (Permanent Marker works well and can removed with alcohol).  Be careful to center the hole (a larger drill bit that just fits within the extrusion, can help mark before using the smaller drill).

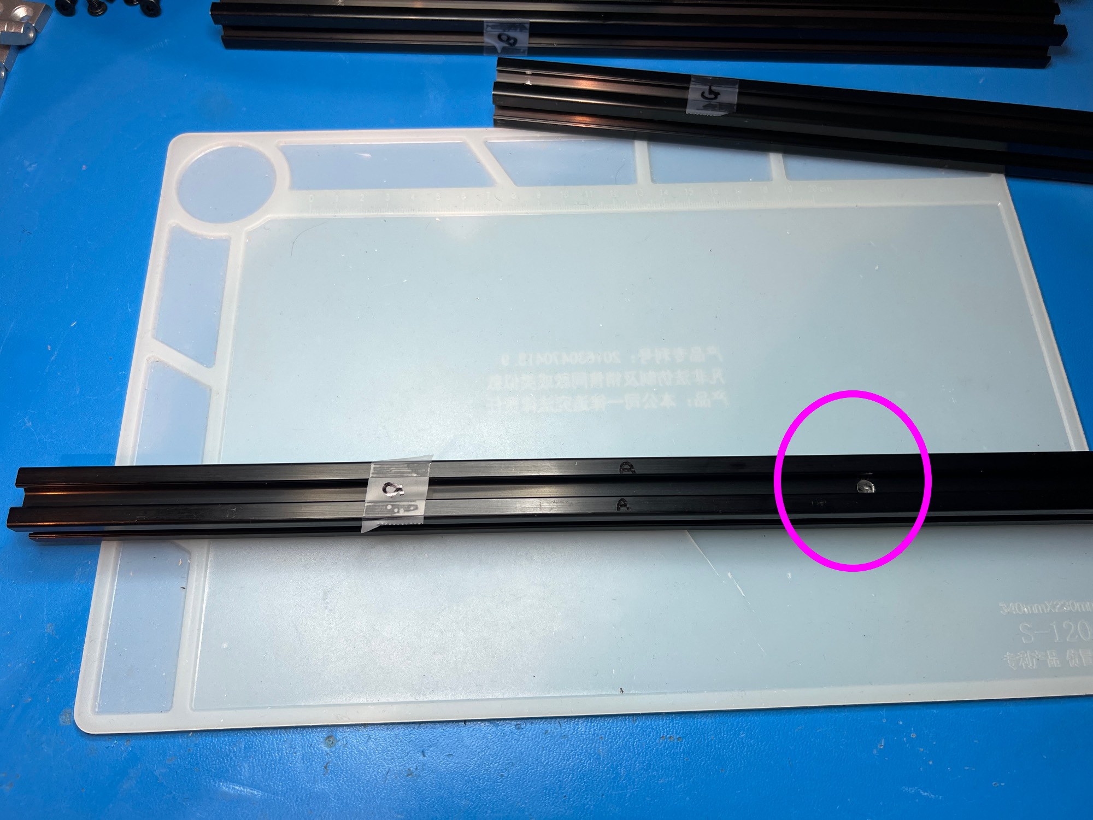
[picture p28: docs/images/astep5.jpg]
Step 5


### Step 6

Take 2 pieces of 360mm profile and drill a 5mm hole 2"/51mm from the end on both pieces.  It is important these holes are centered and straight and not oversized, if you have a drill press, then use that, otherwise drill carefully.  The holes should be in the same place on both pieces, so it may be easier to drill them together.  Label these B and C.

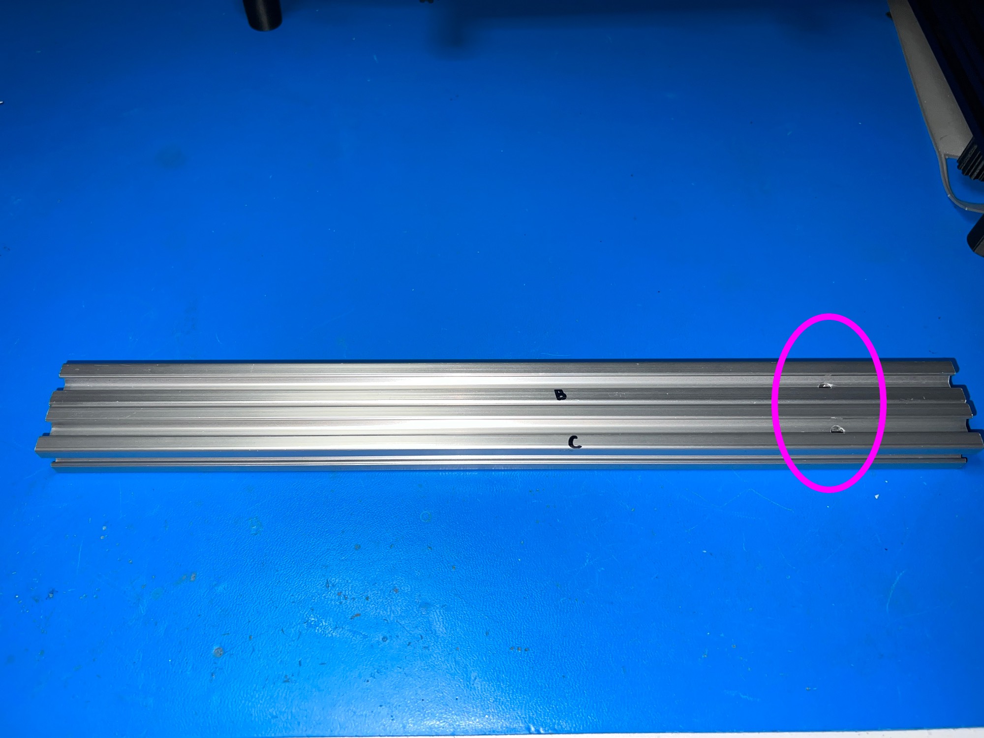
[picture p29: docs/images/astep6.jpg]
Step 6


### Step 7

Take the 270mm profile and drill 2 - 5mm holes 0.5"/13mm in from the ends.  Label this part G.

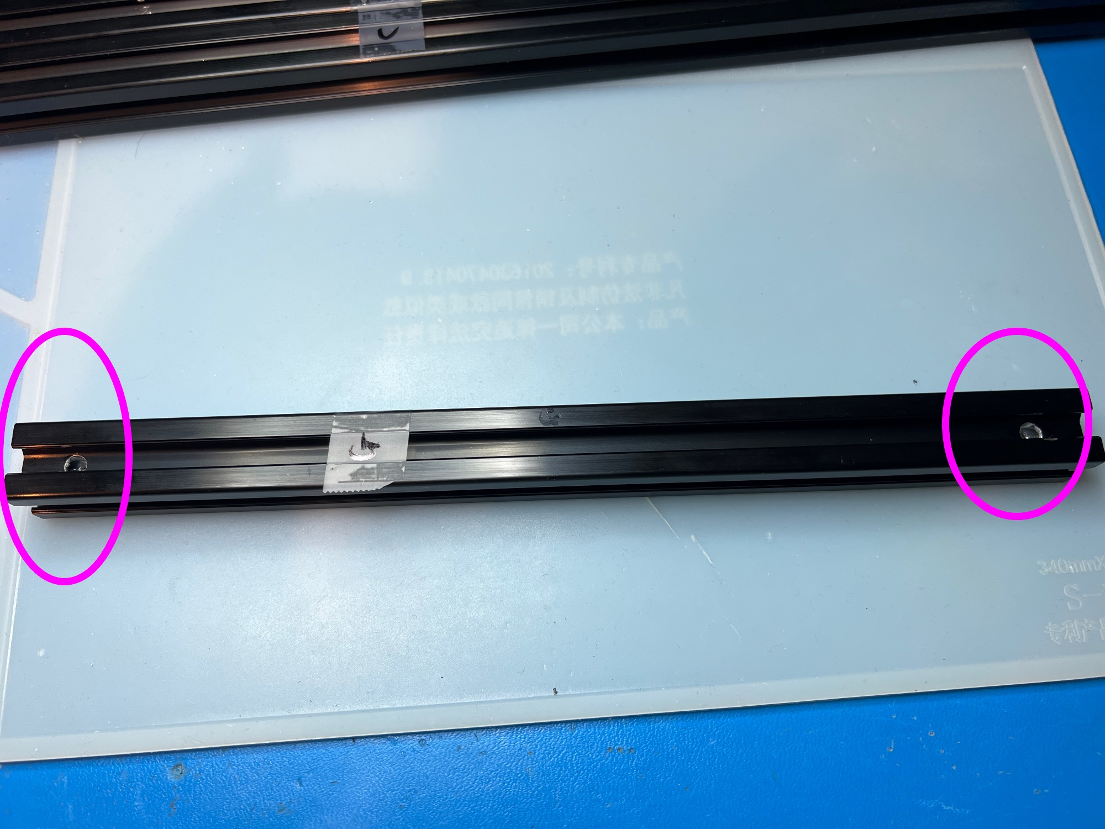
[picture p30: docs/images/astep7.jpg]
Step 7


### Step 8

Take part A and part D and place part A in the center of part D using 2 corner brackets and 4 - T-Nuts / 4 - M5x8mm bolts. The corner brackets have elongated holes and for best rigidity, the bolts should be furthest away from the center of the corner in this hole. It's best to assemble this part of the frame on a flat surface, and only loosely tighten the bolts until you have everything square and flush, then fully tighten.  The hole in part A should be pointing vertically and furthest away from part D.

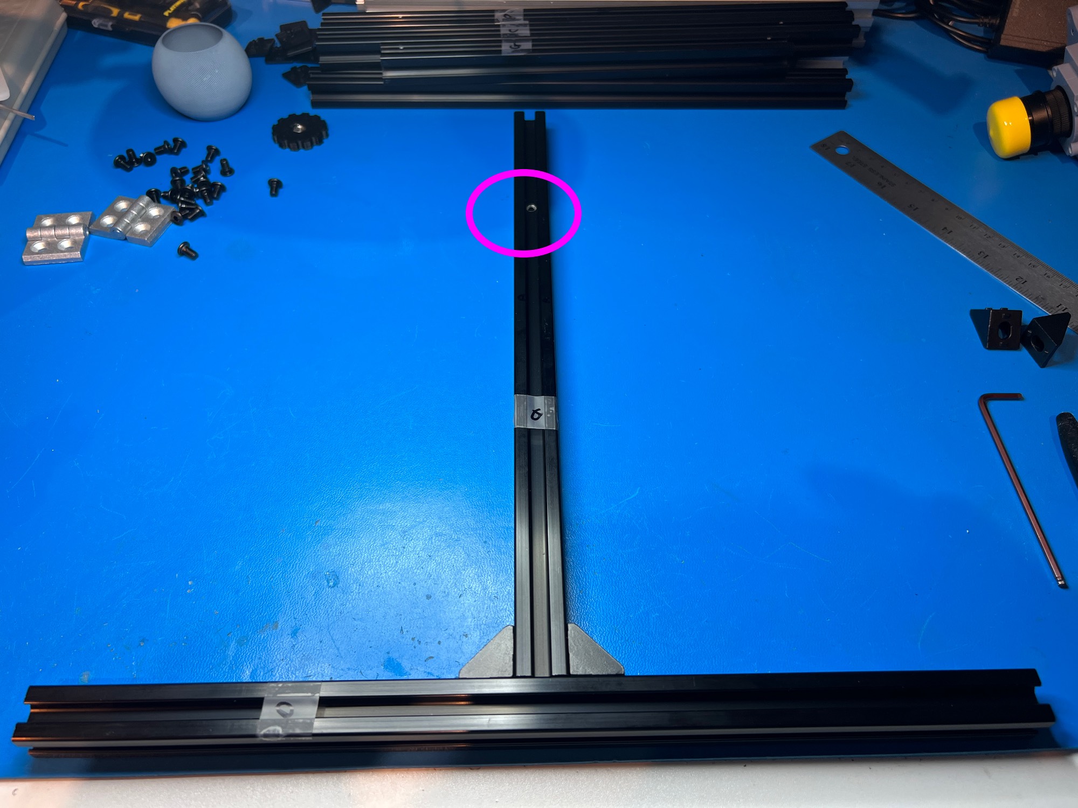
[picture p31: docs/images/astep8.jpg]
Step 8


### Step 9

Repeat step 9 with parts B and E. For this assembly, the hole in part B should be located closest to part E.  Put this assembly on top of the assembly from Step 8 and make sure all parts line up before tightening the bolts down.

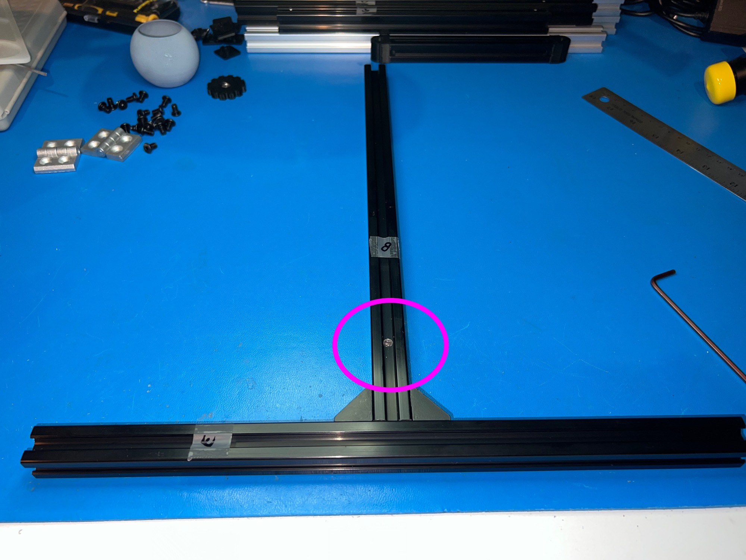
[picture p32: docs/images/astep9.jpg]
Step 9


### Step 10

Take part C and put an end cap on the end closest to the hole, push against a flat surface to put the end cap in.

On a flat surface, insert a T-Nut into the bottom of part B and line up with the hole. Place part C on top and line that up with the hole in part B.  Now take Plate 2 - 13 (Azimuth Rotator) and screw through the top, and bolt B/C together so that it's just friction tight.

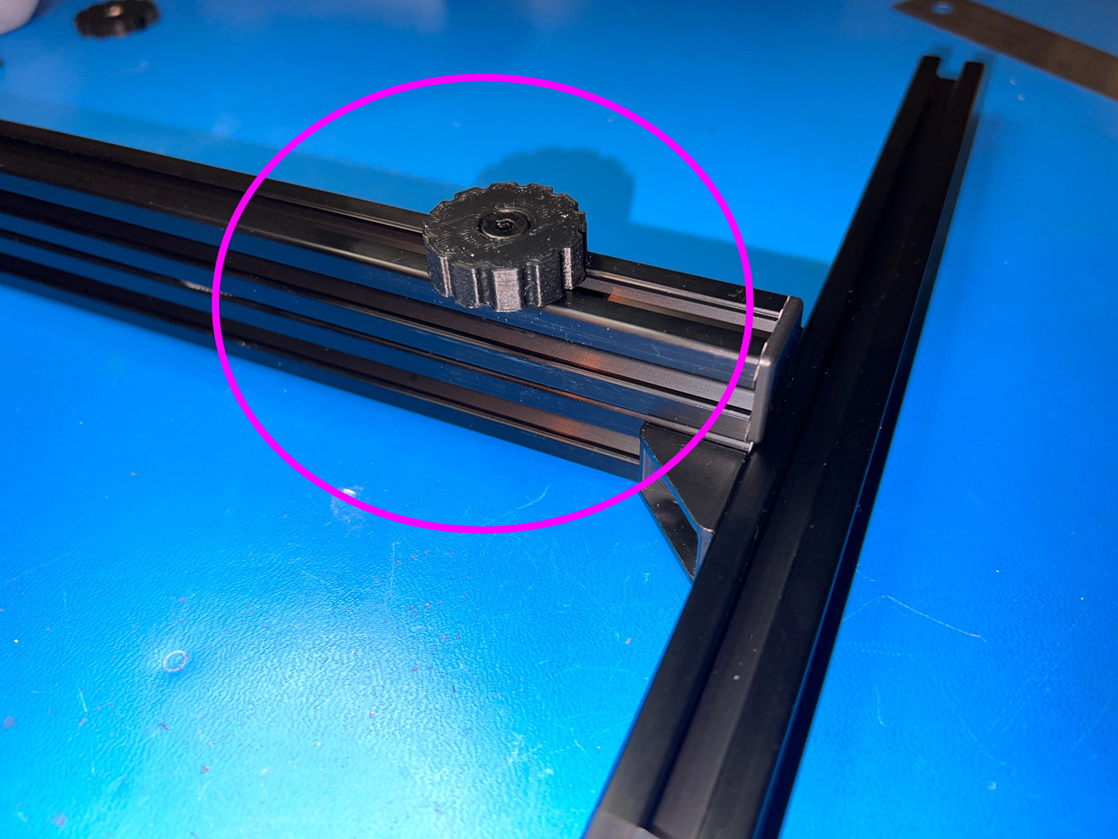
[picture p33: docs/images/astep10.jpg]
Step 10


### Step 11

Locate Plate 2 - 11 (Front FootHolder), and place 2 - M5x8mm bolts into the 2 holes oriented such the the bolt head fits into the recess in the holder.  Now loosely attach 2 - T-Nuts to the bolts.

Insert a T-Nut into bottom of Part A and an additional 2 - T-Nuts into the side (Altitude Marker and the Coarse Altitude Bar), slide on the FootHolder and tighten the FootHolder bolts with the holder flush against the end of the profile.

When correct, the loose T-Nut and the M5 Nut in the foot holder will be orientated on the same side.

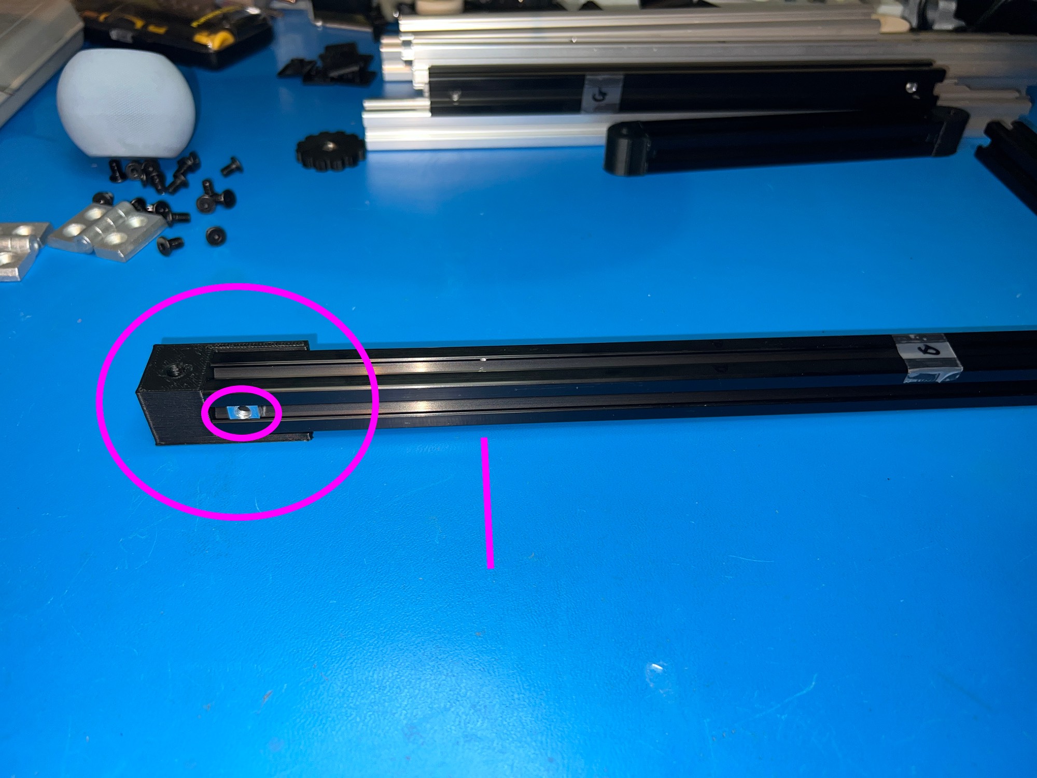
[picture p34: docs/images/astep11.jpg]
Step 11


### Step 12

With the 2 hinges and 8 - T-Nuts and 8 - M5x8mm, put the bolts in the hinges and loosely attach the T-Nuts.

Taking assemblies A/D  and B/E, place B/E on top of A/D and slide in the hinges to the back of parts D and E. It is important to place the hinges at the end (furthest apart) to minimize any twisting motion.

Tighten loosely, and check the movement of the hinge through 90 degrees.  Adjust if necessary before tightening down.  You want to avoid any "play" in the movement.

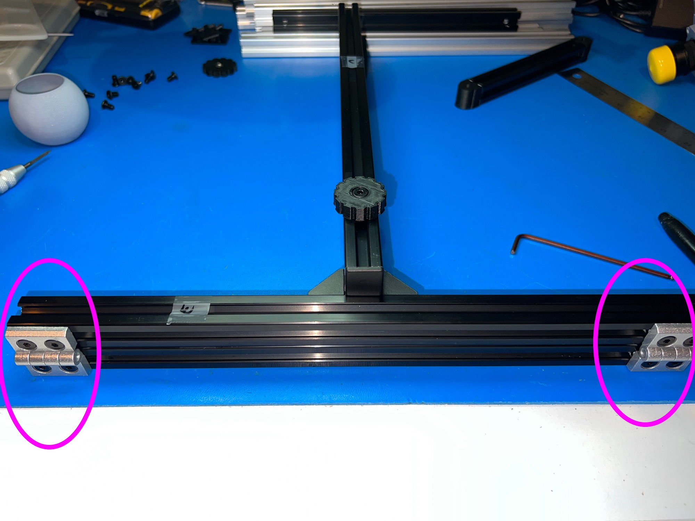
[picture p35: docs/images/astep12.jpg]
Step 12


### Step 13

Locate the azimuth stops (Plate 1 - 1 and 2) and using 4 - T-Nuts and 4 - M5x8mm, place the stops in part E on the top as shown.  Locate the stops such that the front of C does not move past B when moved left to right.

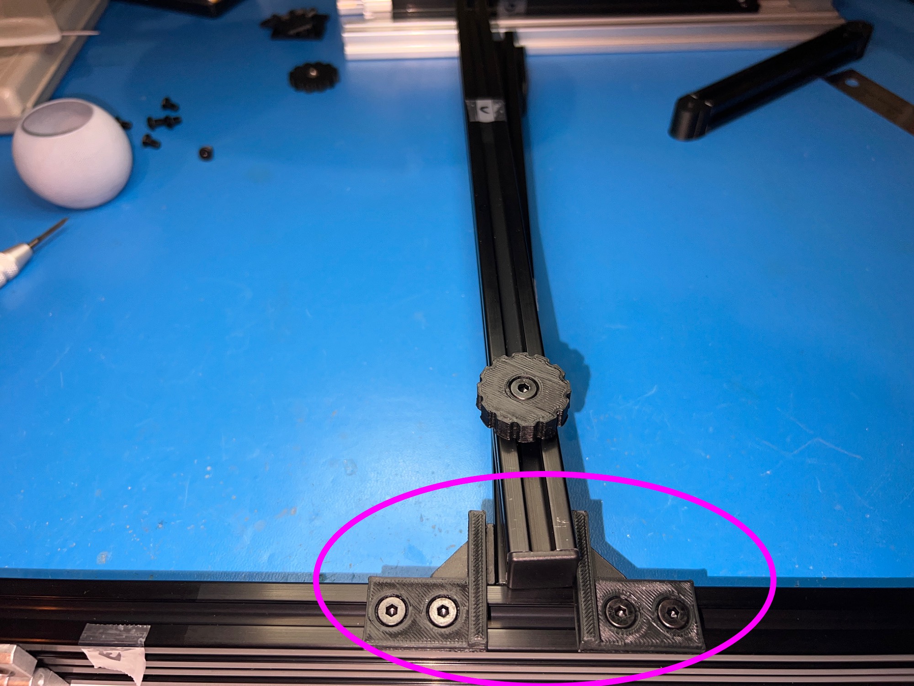
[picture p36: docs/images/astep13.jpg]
Step 13


### Step 14

Take part G and slide a T-Nut over the hole.  Screw part 16 (Extension Bar Foot) in from the same side as the T-Nut.

Place end caps on both ends of part G.

Now place the T-Nut in the bottom of part D and using part 14, bolt through G into the T-Nut.

Fold part G so that it's inline with part A and tighten gently.

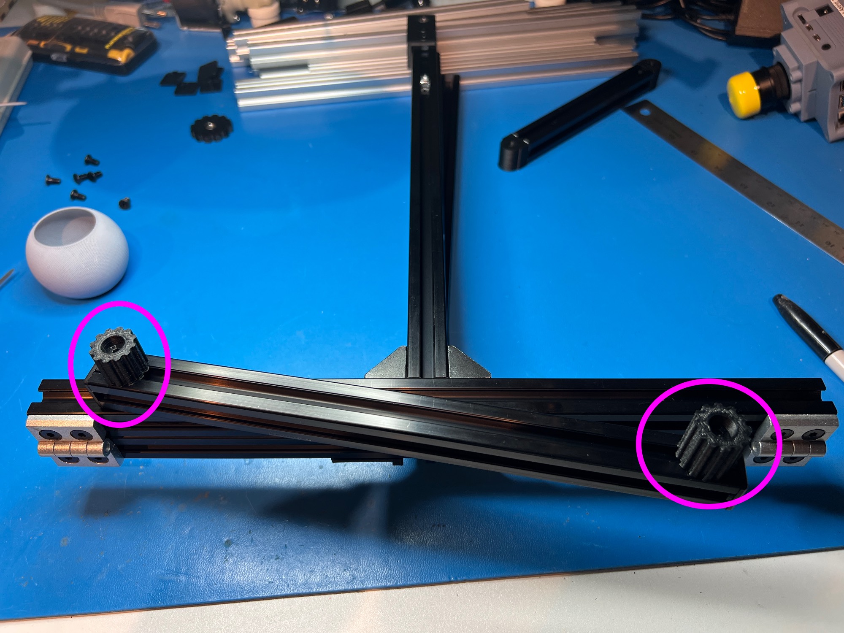
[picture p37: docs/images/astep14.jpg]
Step 14


### Step 15

Assemble Plate 1 - 4 (Rear Foot x 2) with a M5x8mm bolt and a T-Nut.  Slide these 2 feet onto the ends of part D and finger tighten.

Screw Plate 1 - 5 (Front Foot Lock) onto Plate 2 - 12 (Front Foot) and then screw into the FootHolder at the front of Part A.

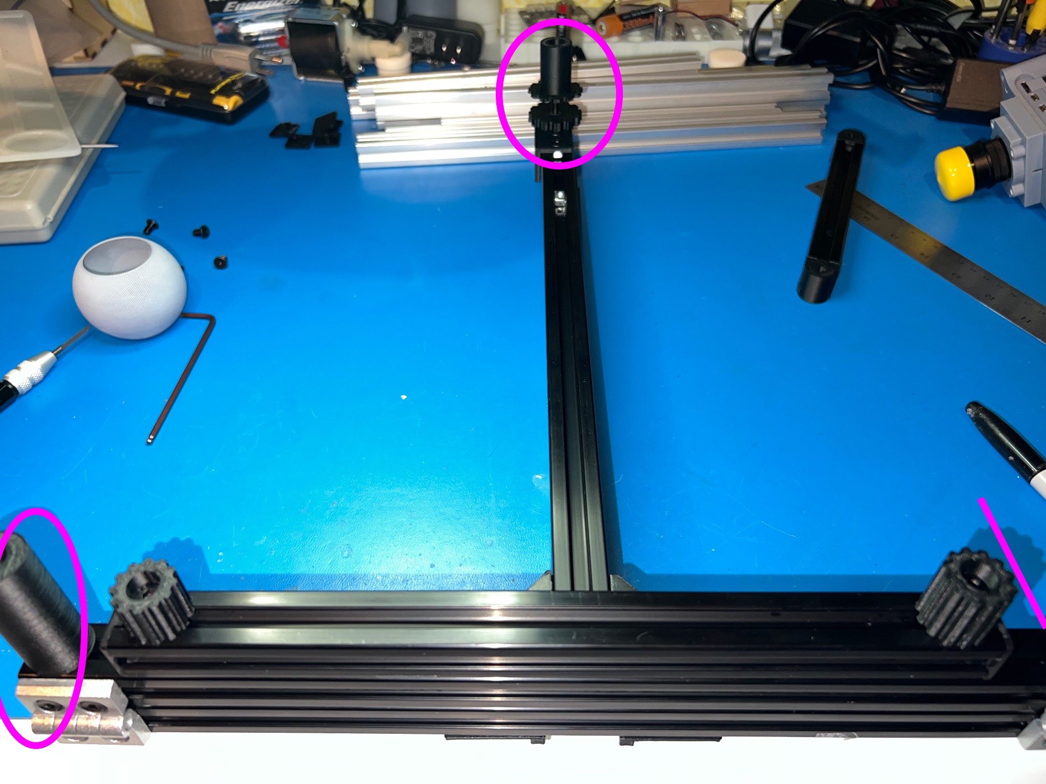
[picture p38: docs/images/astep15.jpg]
Step 15


### Step 16

Insert a T-Nut into part B.  With part F (Coarse Altitude Bar), use Plate 2 - 10 (Altitude Knobs x2) to bolt through the holes in the bearing into the T-Nuts and tighten loosely. Note, the T-Nut used on part A should be the rightmost T-Nut.  Orient the smoothest side of the bearing towards parts A/B.

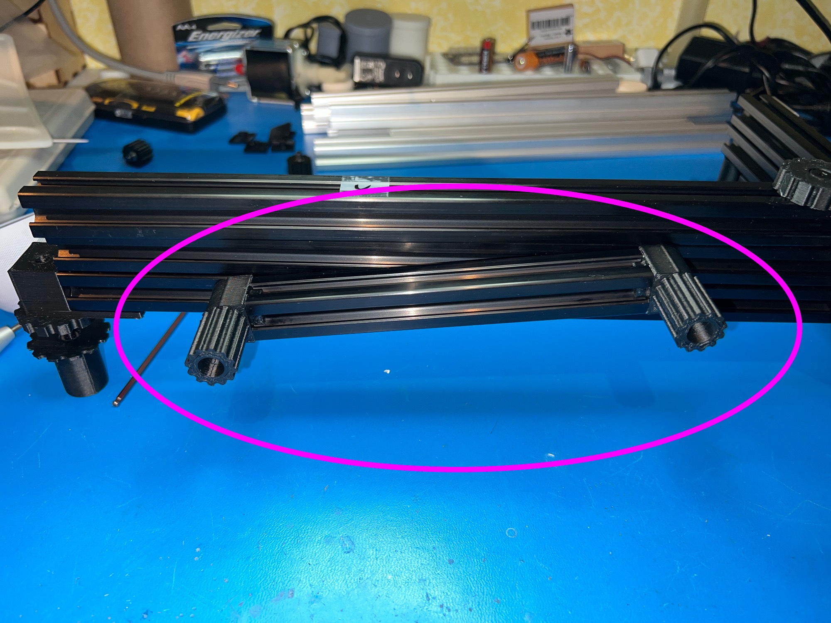
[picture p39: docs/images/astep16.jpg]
Step 16


### Step 17

Insert a T-Nut into part B.  Locate parts Plate 1 - 3 (Altitude Markers x2) and parts Plate 2 - 15 (Altitude Marker Knobs x 2), and push the knob through the marker and bolt into the T-Slot as shown.

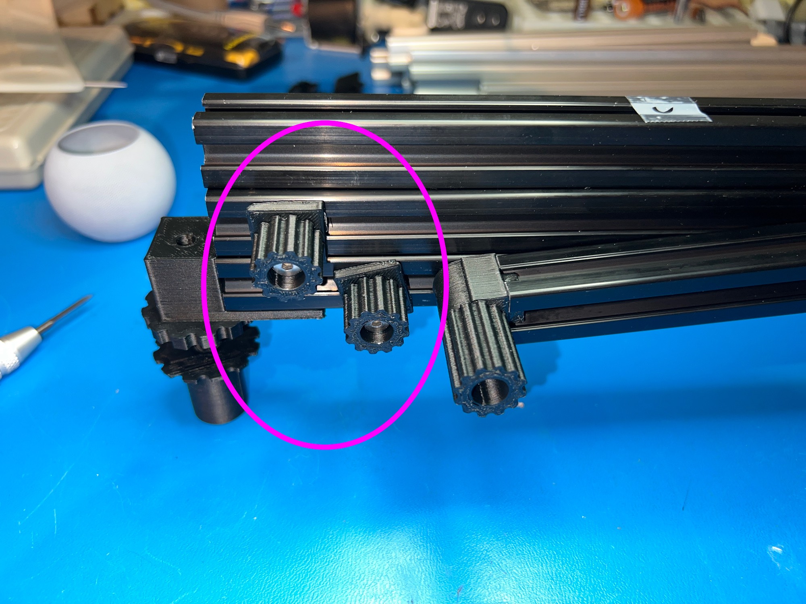
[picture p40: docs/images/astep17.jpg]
Step 17


### Step 18

If using the Orion ST 80mm, locate parts 20 and 21 and using 4 - T-Nuts and 4 - M5x8mm, assemble and slide into the top of part C as shown, place scope on top, adjust and then tighten down. Note part 20 (widest groove) goes at the front.  Locate parts 23, and using permanent double sided tape on the curved side, attach to the scope such that the scope slides down against part 21 and rests when the mount is at higher elevations.  The scope should also be held down with either rubber bands or the 3d-printed NinjaFlex or TPU bands.

If using the 1/4" Mount, use 2 - T-Nuts and 2 - M5x8mm and slide into the top of part C.

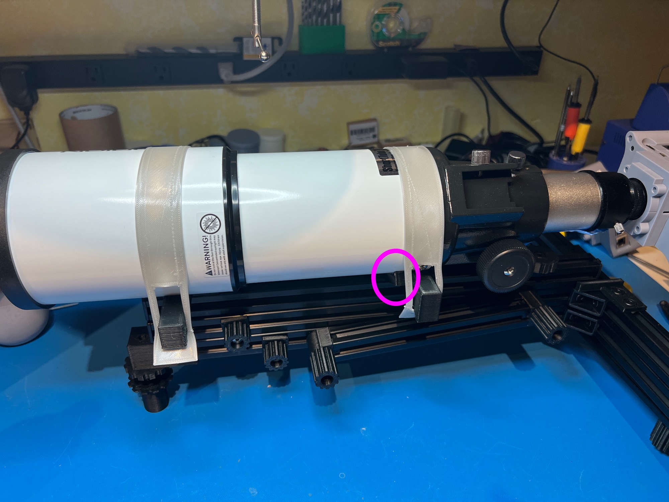
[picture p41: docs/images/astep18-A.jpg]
Step 18 - A

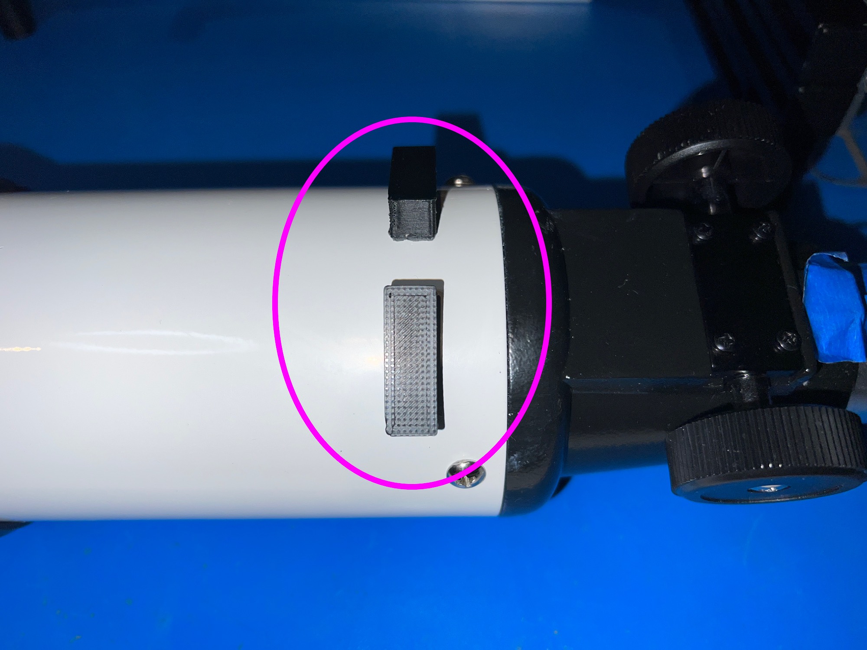
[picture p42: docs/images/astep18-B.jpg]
Step 18 - B


### Step 19

Insert remaining end caps.

### Step 20 (Optional)

If using a paver to place the mount on, parts Plate 1 - 6 (Paver Registrations) can be glued to the paver as shown using Super Glue or Epoxy for repeatability in positioning.  The L shaped piece goes in a corner, and the straight piece at the opposite end of the adjacent edge to the corner piece.

Paver Registration

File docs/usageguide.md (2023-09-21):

# Usage Guide

### Work in progress, more to come!

## Regular Deployment

A regular deployment is a deployment where the user pre-points the occultation for a particular event time and the star moves into view at the time of the occultation. This type of deployment may use a wooden square, paver, concrete pad, or other hard non-moving/settling surface to set up on.

It is recommended to carry a 5mm Allen Key for deployments incase something needs tightening.

Describe mount setup and adjustments.

## Pre-point Later

"Pre-point Later" deployments are set ups, where a platform (typically paver or staked plywood) is put in a location days in advance and the scope is pre-pointed to the location of the event. Then the telescope/mount are removed and brought back and deployed on the day of the event.  These set ups are more challenging, as the user has to be careful to restore everything to the exact same position.

The mount configuration is similar to the [Regular Deployment](#regular-deployment) detailed above, with the addition of steps to record the current telescope position and location on the platform.

## 12" Paver Deployment

Describe paver registration and foot reversal, also describe with and without feet.

## >=16" Paver Deployment (or Staked Plywood)

Same as 12" but without the foot reversal.

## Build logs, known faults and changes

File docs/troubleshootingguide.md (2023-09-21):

# Troubleshooting Guide

## Fine Azmiuth Adjustment Too Loose

Depending on the 2020 extrusion, the fine azimuth adjustment may be too loose.  Often a simple solution is to invert part C.  However, if that doesn't work, a small piece of adhesive 1mm felt at the end will provide the needed additional friction.

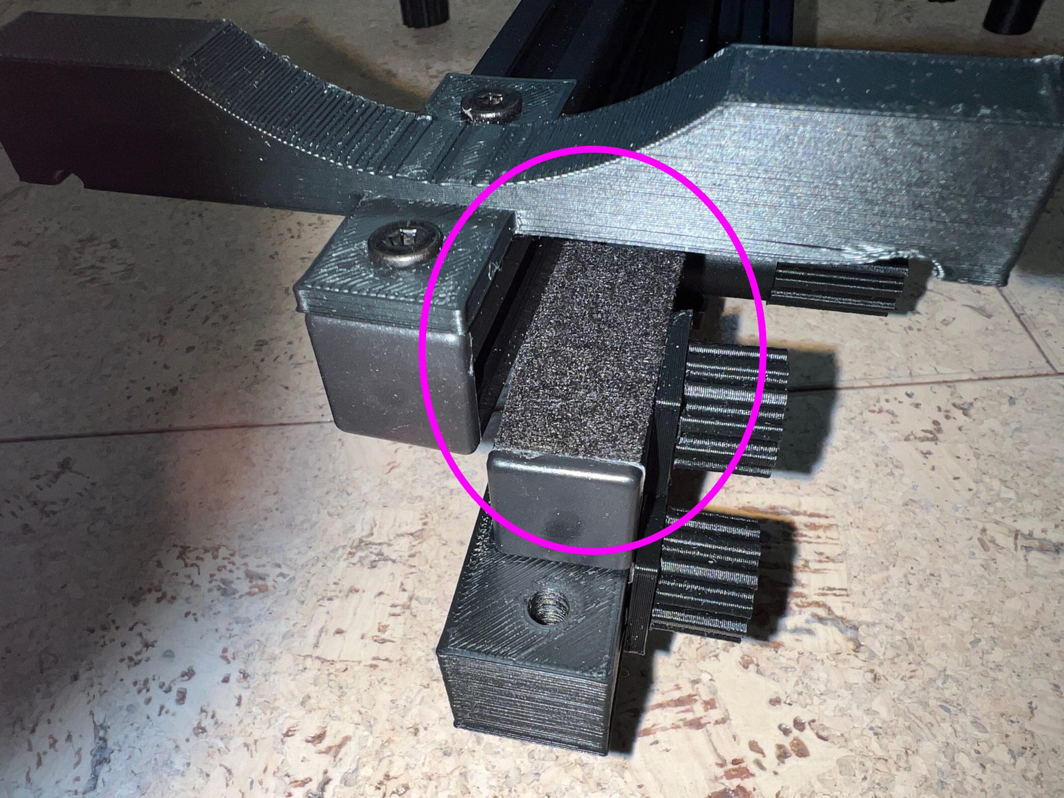
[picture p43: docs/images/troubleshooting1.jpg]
Felt Pad


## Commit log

2023-09-18 Renaming to TSlotBroughtonMount and expanding documentation
    [TSlotBroughtonMount.scad]
2023-09-18 Slide stop for telescope. Brackets for paver registration. Altitude Markers for altitude bar repositioning.
    [TSlotBroughtonMount.scad]
2023-09-19 Updating documentation
    [TSlotBroughtonMount.scad]
2023-09-19 Checking in stl files, adding quarter inch mount and adding parts images
    [TSlotBroughtonMount.scad, mountBandsOrionST80.stl, mountQuarterInch.stl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]
2023-09-20 Updating assembly guide
2023-09-20 Adding assembly pictures
2023-09-20 Adding step 1 photo to the assembly guide
2023-09-20 Updating README
    [maggpsholder.scad, maggpsholder.stl]
2023-09-20 Moving gps antenna folder
    [maggpsholder.scad, maggpsholder.stl]
2023-09-21 Too many screws for mag antenna, fixing
    [maggpsholder.scad]
2023-09-24 Added 2 to the M5x8mm screw count. Minor correction to assembly guide.
2023-11-08 Reinforced Foot and Foot Holder
    [TSlotBroughtonMount.scad, plate1.stl, plate2.stl]
2023-11-09 Adding new Battery Platform Addon.
    [TSlotBroughtonMount.scad, batteryplatform.scad, batteryplatform.stl]
2023-11-09 Updating main README to include information about the Battery Platform
2023-11-09 Reordered the Battery Platform reference
2023-11-10 Reducing tolerance on Altitude Foot. Clarifying documentation with 2020 Cut Summary
    [TSlotBroughtonMount.scad, plate2.stl]
